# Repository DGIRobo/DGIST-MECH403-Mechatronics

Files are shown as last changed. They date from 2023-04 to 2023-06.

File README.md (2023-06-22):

# Pen Plotter for Blind People

**DGIST Undergradurate Student Jihwan Lee**

**DGIST Undergradurate Student Minhyeok Baek**

*Daegu Gyeongbuk Institute of Science and Technology (DGIST) Spring semester*

# **i**. Introduction

---

### 1. Project Topic:

시각장애인이 일반인들을 위해 제공되는 자료를 읽고 쓰게 할 수 있는 서비스를 제공하기 위한 음성기반 상호작용이 가능한 Pen Plotter의 개발.

### 2. Project Background:

지금까지 점자표지판, 점자 민원, 말하는 간행물 등 시각장애인을 위한 많은 서비스들이 만들어져 왔고, 이러한 서비스들은 실제로 공공기관에서 활용하고자 적극적으로 도입되어 왔습니다. 하지만, 이러한 대부분의 서비스는 사용자들을 배려하지 않아 완성도가 떨어지거나 공공기관에 도입한 이후에 제대로 서비스를 유지하고 관리하지 않아 사실상 활용도가 크게 떨어지는 문제점들을 가지고 있었습니다.

- 선행연구 1: 인쇄물음성변환출력코드(‘보이스아이’)
    
    말하는 공문서, 말하는 간행물과 같은 경우, 공공기관이 발행되는 간행물에 문서에 담긴 글과 미디어파일 등을 압축 저장한 일종의 바코드인 인쇄물음성변환출력코드(일명 ‘보이스아이’)를 첨부하여 제공하면, 시각장애인이 전용 스캐너를 사용해서 이 코드를 스캔해서 제공된 글이나 미디어를 볼 수 있게 해주는 서비스입니다. 이 서비스는 2009년 기준 대한민국 전자정부(G4C) 인터넷 민원서류 130여종과 보건복지부, 문화체육관광부 등 정부부처, 헌법재판소, 국가인권위원회, 서울시청, 서울 강남, 송파, 용산, 종로구청, 부산시청, 제주도청에서 도입되었고 전기요금고지서와 서울시수도요금고지서, 전국 지방세 고지서에서 사용되고 있다고 합니다. 하지만 이 서비스는 2009년 CBS 뉴스와 한국장애인문화협회 소리샵 센터가 공동 비교 분석한 결과 애당초 코드 자체가 읽히지 않거나 시각장애인들이 이해하기 어려울 정도로 잘못 편집된 경우가 많았다고 합니다. [1]
    
- 선행연구 2: 점자민원 서비스
    
    또한 점자 민원과 같은 경우, 공공기관이 발행되는 일반 간행물의 문서에 담긴 글과 미디어파일 등을 점자로 번역하여 시각장애인을 위한 간행물을 따로 제공하면, 시각장애인이 이 점자를 통해 제공된 글이나 미디어를 읽어볼 수 있게 해주는 서비스입니다. 이 서비스는 2016년 만들어진 점자법에 따라 현재 전국의 모든 공공기관이 도입하고 있습니다. [2]
    
    하지만 2020년에 진행된 대구대학교 한국특수교육문제연구소의 연구에 따르면 많은 시각장애인들은 이 서비스에 대해 잘 인지하고 있지 못하고 있고, 심지어 알고 공공기관에 요청함에도 불구하고 서비스를 받을 수 없었다고 합니다. [3][4]

때문에 이런 많은 서비스가 있음에도 불구하고 현재까지 시각장애인들은 보조인을 대동하여 민원 신청을 하거나 본인에게 필요한 정보를 찾아보는 것이 대한민국의 시각장애인의 현실입니다.

### 3. Problem Statement:

한 문장으로 정리하면, 공공기관에서 정보를 시각장애인이 인지할 수 있게 많은 서비스를 제공중임에도 시각장애인들은 공공기관의 홍보가 부족하여 이런 서비스들을 인지하지 못하고 있거나, 심지어는 공공기관에서 시각장애인들을 위한 서비스를 적절하게 제공하지 못하고 있는 문제로 인해 시각장애인들은 기본권인 “국민이 정부에 대한 일반적 정보공개를 구할 권리(청구권적 기본권)”과 “주민이 행정 기관에 원하는 바를 요구하는 일(민원)”을 보장받지 못하고 있습니다.

### 4. Approach:

따라서 우리는 공공기관에서 정보를 시각장애인이 인지할 수 있게 이런 많은 서비스를 제공중임에도 제대로 활용되고 있지 못하는 현 상황을 타개하고자. 시각장애인이 일반인들을 위해 제공되는 자료를 로봇을 통해 대리로 읽고 쓰게 할 수 있는 서비스를 만들고자 합니다.

- For Reading
    
    시각장애인이 일반인들을 위해 제공되는 자료를 로봇을 통해 대리로 읽고 쓰게 할 수 있는 서비스를 만들기 위해 우리는 우선 제공되는 자료를 카메라를 통해 보고 이것을 시각장애인이 받아들일 수 있는 감각을 통해 전달하는 기능이 필요하다는 것을 생각했습니다.
    
    일반적으로 시각장애인에게 정보를 전달할 수 있는 수단이라 하면, 대부분 점자와 음성을 떠올릴 것입니다. 하지만 한국의 점자 사용실태에 대해 추가로 조사한 결과, 한국시각장애교육&재활학회에서 발표된 조선대학교의 2015년 연구에서 표본 1000명 중 60%에 가까운 584명이 점자 사용을 하지 않고 있다는 것과, 이 중 100명은 음성지원 보조공학기기를 선호해서, 200명은 점자가 너무 어렵고 읽는 속도가 느려서 사용하지 않고 있다는 것을 확인하였습니다. 이 조사결과를 참고하여 시각장애인이 더 선호하는 음성서비스를 채택하기로 하였습니다. [5]
    
- For Writing
    
    시각장애인이 일반인들을 위해 제공되는 자료를 로봇을 통해 대리로 읽고 쓰게 할 수 있는 서비스를 만들기 위해 우리는 다음으로 시각장애인과 소통하여 시각장애인의 요구를 글로써 적을 수 있는 기능이 필요하다는 것을 생각했습니다. 일반적으로 시각장애인의 요구를 글로써 적을 수 있는 수단은 대부분 프린터를 떠올리겠으나 프린터는 단독적으로 사용될 수 없고 유지 보수에 있어서 많은 비용이 들기 때문에 부적합하다고 판단했습니다. 이 점으로 미루어볼 때, 유지 보수에 큰 비용이 들지 않는 저예산의 로봇팔을 채택하기로 하였습니다.

따라서 우리는 구체적으로 글자를 인식할 수 있는 카메라와 글자를 쓸 수 있는 펜 로봇을 조합하고, 음성기반 상호작용이 가능한 Pen Plotter라는 제품을 개발하는 접근법을 통해 이 문제를 해결하고자 했습니다.

# **ii**. Method

---

# 1. Hardware Design

Pen Plotter는 다음과 같이 설계되었습니다.

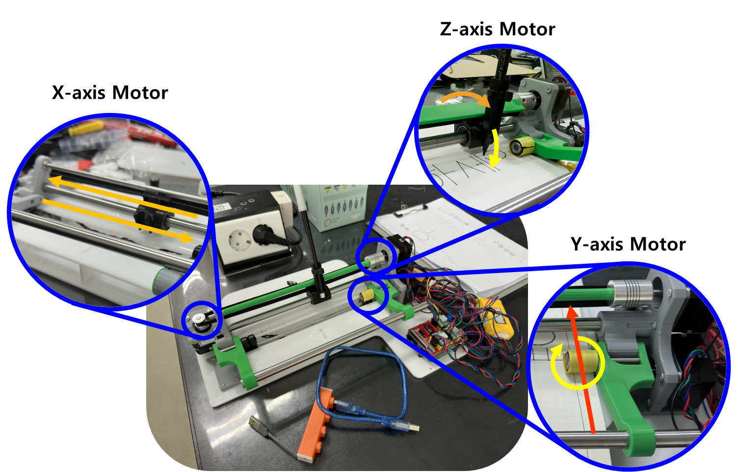
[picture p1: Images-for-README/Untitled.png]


기존의 x-y axis를 이동하는 Pen Plotter와는 다르게, y축 움직임을 롤러로 대체하여 공간의 컴팩트함을 강조하였습니다. 또한 모든 몸체와 하우징을 3D프린터와 레이저커터를 사용해 조립 가능한 형태로 제작함으로써, 교체 및 수리의 용이성과 제작의 간편함을 추구하였습니다. 바닥면의 경우 아크릴을 사용하여 바닥과의 마찰을 최소로 함과 동시에 평탄함을 잡았습니다. 각 구조에 대해 디테일하게 설명하도록 하겠습니다.

## 1-1) Base design

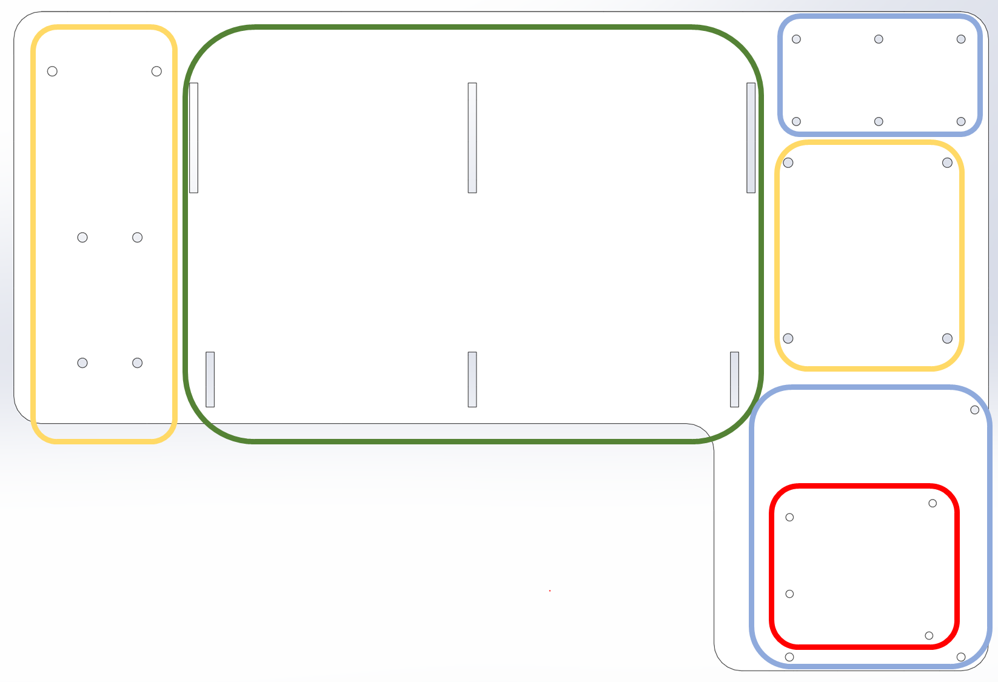
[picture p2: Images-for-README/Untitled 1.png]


 틀이 되는 베이스 부분입니다. 기본적으로 조립이 용이하도록 타공 형식으로 나사를 체결할 수 있도록 제작하였으며, 제일 basic한 M3 나사로 체결합니다. 실제 조립에는 진동이나 기타 이동으로 풀리지 않도록 spring washer를 사용해 진동 및 기타 disturbance에 영향을 받지 않도록 조립하였습니다.

각 타공된 구멍에 따른 역할은 다음과 같습니다.

> Yellow: Plotter base
Green: Paper base
Red: Circuit hole
Blue: Wire holder+Case
> 

3mm 아크릴로 제작하였으며, E5의 레이저커터를 사용해 제작했습니다.

## 1-2) X-axis side

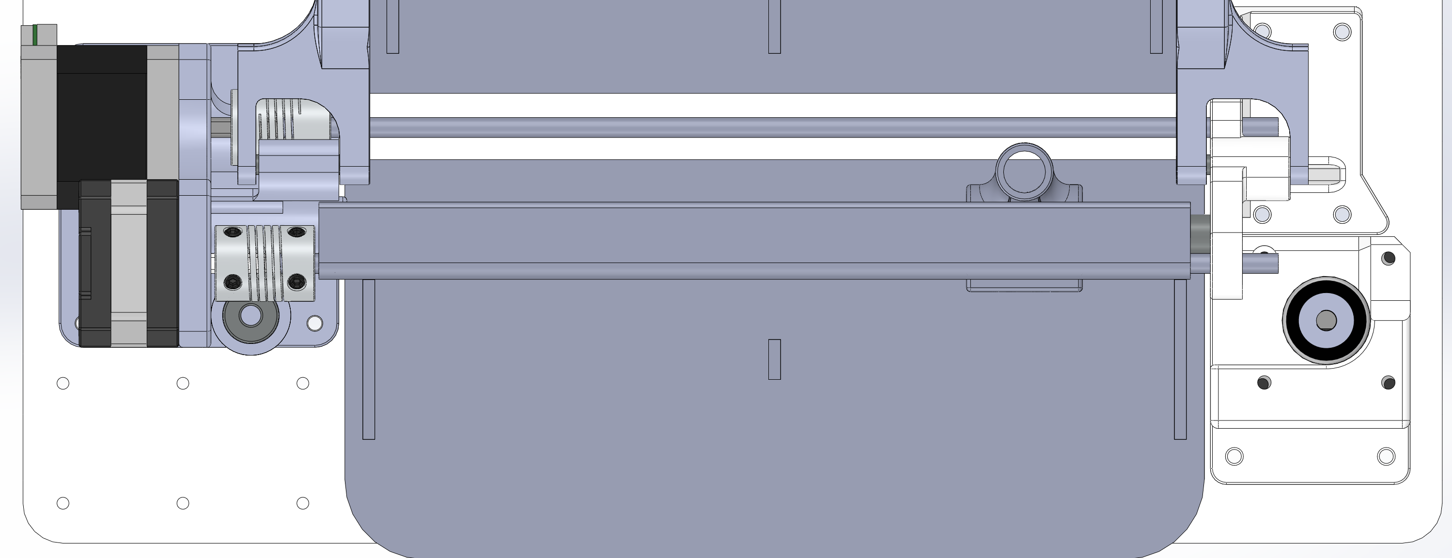
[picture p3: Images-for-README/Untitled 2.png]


X축의 경우, belt를 사용한 일반적인 plotter의 방식을 사용하였습니다. belt만 가지고는 고정력이 부족하기 때문에, 10mm 연마봉을 사용하여 pen을 지지하였습니다. 이 경우 연마봉과 pen 지지대 사이의 마찰력이 움직임에 영향을 줄 수 있기 때문에, ball bush를 사용하여 마찰력을 상쇄하였습니다.



Belt와 pen 지지대는 M3 나사로 체결하여 나사가 belt를 눌러주어 이동에 영향이 가지 않도록 디자인하였습니다.

X축의 최소 이동 거리의 경우, NEMA 17모터의 최소 step이 1.8도이고, 사용한 풀리의 잇수가 20입니다. 따라서 이를 계산하여 보면, 250step 기준으로 1.25바퀴를 회전하게 되고, 이는 25잇수만큼의 회전입니다. 부품의 각 이 간 거리가 2mm이므로, 250step : 50mm = 1step : xmm 를 계산하여 보면 1step = 0.2mm로 계산됩니다. 따라서 x resolution의 최소 단위는 0.2mm임을 알 수 있습니다.

## 1-3) Y-axis side

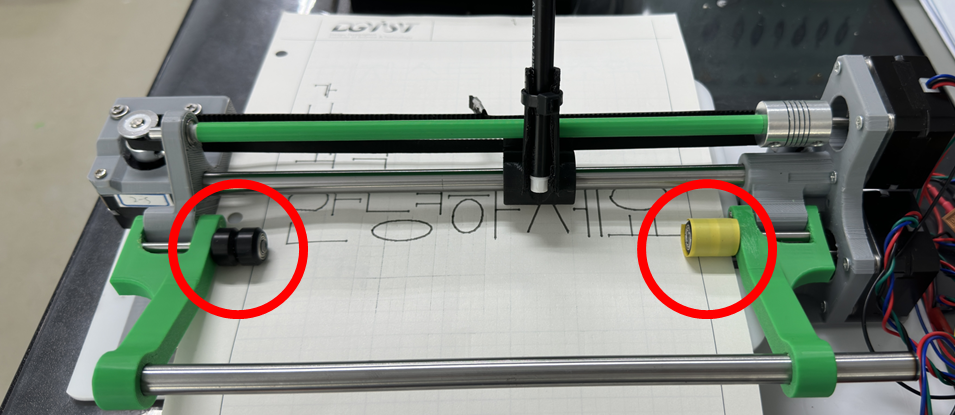
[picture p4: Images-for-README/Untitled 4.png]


Y축의 경우, roller를 사용하여 종이를 밀어주는 일반 잉크젯 프린터와 같은 방식을 차용하였습니다. roller는 저가 3D프린터에 주로 사용하는 roller bearing을 사용하였고, 단단한 고정 및 이동을 위해 양쪽에 2개씩, 위 아래로 한 쌍, 총 8개를 사용하여 종이를 단단하고 일정하게 밀어줄 수 있도록 하였습니다. 또한 손잡이를 10mm 연마봉으로 지지함으로써, 지레의 원리로 종이를 무겁게 눌러줌으로써 slip으로 인한 disturbance를 방지합니다.

그럼에도 실제 테스트 시에 종이가 slip하지 않을까 걱정되었지만, 사람이 잡고 있는 손이 끌려들어갈 만큼 slip은 충분하였습니다.

## 1-4) Z-axis side

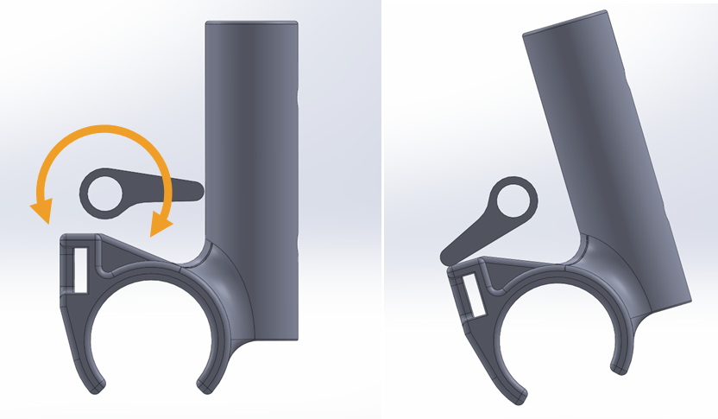
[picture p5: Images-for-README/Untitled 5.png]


기존의 돌기를 Z-axis의 lifter가 밀어 펜을 움직이는 방식과 달리, pen 자체를 밀어 움직이도록 하였습니다. 따라서 디자인의 컴팩트함을 더 올렸고, 단순히 belt의 tension으로 pen을 원위치 시키는 것이 아닌 두번째 사진처럼 종이에서 떨어질 때에는 반대방향으로 회전하여 pen을 고정시킴으로써 pen이 앞으로 쏠려 종이에 닿거나 진동으로 인해 종이에 닿는 상황을 막아줍니다. 이는 출력부의 회전을 고정시켜 출력시에 더 안정적으로 이동할 수 있게 해줍니다.

## 1-5) Other details

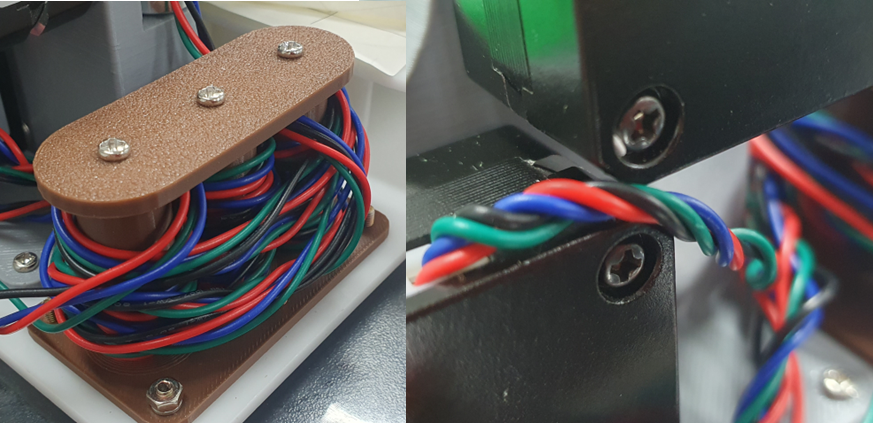
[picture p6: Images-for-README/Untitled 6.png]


뒷 부분에는 긴 wire들을 수용할 수 있도록 wire holder를 제작하였습니다. 세 축(X Y Z)의 전선들을 각각 수용할 수 있어 추후 점검이나 부품 교체에 용이하도록 설계하였습니다. 이 역시 spring washer로 조립되어 안정성을 높였습니다. 각 wire들은 unshielded twisted pair로 꼬아 놓음으로써 발생할 수 있는 noise나 간섭에 대해서도 보강하였습니다.

또한 본 시스템의 경우 CNC나 여타 pen plotter에 사용되는 endstop switch가 존재하지 않습니다. 이는 의도한 것으로, endstop 스위치가 가지는 불편한 점을 개선하기 위해 일부러 넣지 않았습니다. 이에 대한 이유는 Software design의 Gcode 부분에서 서술하겠습니다.

# 2. Software Design

다음으로 위와 같은 Hardware를 구동하는 Software는 아래 그림과 같이 설계되었습니다. 

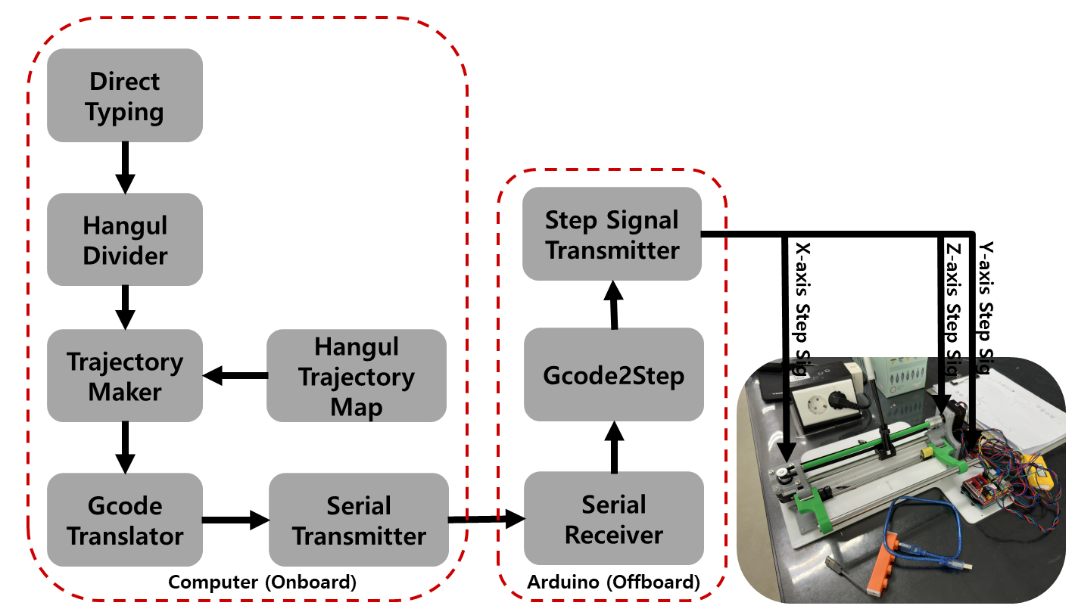
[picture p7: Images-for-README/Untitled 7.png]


전체적인 Algorithm을 요약해서 설명하자면 다음과 같습니다. 사용자가 컴퓨터에 키보드를 이용해서 한글 문장을 입력하면 Computer는 그 한글 문장을 자모 단위까지 분리하고 자모 Trajectory를 참조해서 글자 하나부터 문장까지 정규화된 계산 방식을 사용해서 차근차근 결합시켜서 하나의 Trajectory를 만들어냅니다. 그리고 Computer는 이 Trajectory를 Gcode 양식으로 변환해서 Serial 통신을 통해 Arduino에 송신합니다. 그러면 이제 Arduino는 Computer로부터 Serial 통신을 통해 들어온 Gcode 양식의 Trajectory를  Step 단위로 바꿔서 각 X축, Y축, Z축 Step 모터를 해당 Step 만큼 움직이는 것을 제어하는 것으로 사용자가 입력한 문장을 A4 종이에 대필하는 것을 수행할 수 있게 됩니다.

이때 설명한 Computer가 수행하는 구체적인 연산은 모두 객체화되어 있습니다. 첫번째로 사용자가 입력한 한글 문장을 한글의 자모 단위까지 분리하고 한 글자 마다 Type을 부여하는 Algorithm은 Hangul Divider라는 이름으로 객체화되어 있습니다. 두번째로 자모 데이터를 참조해서 자모 Trajectory를 추출하는 Algorithm은 Hangul Trajectory Map이라는 이름으로 객체화되어 있습니다. 세번째로 자모 Trajectory를 조합해서 한 문자, 한 단어, 문장까지 이어서 조합하는 Algorithm은 Trajectory Maker라는 이름으로 객체화되어 있습니다.

## 2-1) Hangul Divider Algorithm

앞서 소개했듯 사용자가 입력한 한글 문장을 한글의 자모 단위까지 분리하고 한 글자 마다 Type을 부여하는 Algorithm은 Hangul Divider라는 이름으로 객체화되어 있습니다. 이 Hangul Divider는 [6]에서 소개하는 Algorithm을 펜 플로터 Trajectory 생성을 위해 Concept만 반영하고 다르게 구현된 방식입니다. [6]의 설명에 따르면 한글 unicode에는 아래 사진과 같은 규칙이 있습니다.

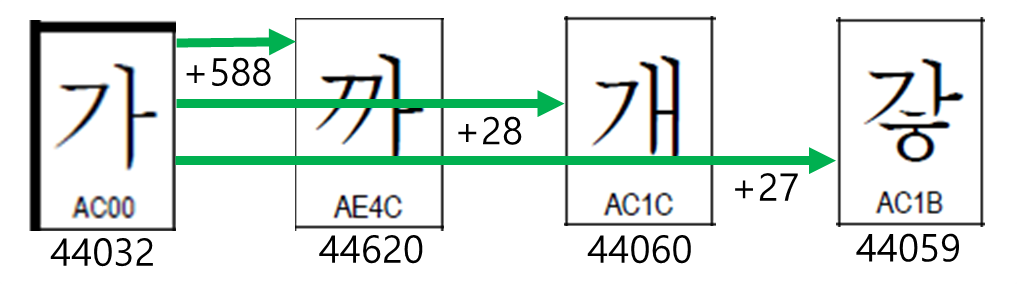
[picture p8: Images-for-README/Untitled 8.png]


우선 한글 unicode는 초성이 588 문자마다 바뀝니다. 이는 즉 한글 unicode를 588로 나누면 그 한글의 초성을 추출할 수 있다는 것을 의미합니다. 또한 한글 unicode는 중성이 같은 초성일 때 28 문자마다 바뀝니다. 이는 즉 한글 unicode에서 초성을 추출한 후 unicode에서 초성값에 588을 곱한 값을 빼주고 28로 나누면 그 한글의 중성을 추출할 수 있다는 것을 의미합니다. 종성도 마찬가지로 초성과 중성이 같을 때 28개가 존재합니다. 따라서 한글 unicode에서 초성을 추출한 후 unicode에서 초성값에 588을 곱한 값을 빼주고 중성값에 28을 곱한 값을 빼주고 28로 나누면 종성을 추출할 수 있습니다. 따라서 Hangul Divider Algorithm은 이를 반영하여 입력된 문장을 글자 하나 하나로 나누고 글자 하나 하나를 초성 중성 종성으로 또 한번 나눕니다.

거기에 Hangul Divider Algorithm은 Trajectory 형성을 위해 한글의 형태에 대한 정보를 분리한 초성 중성 종성 정보에 추가하여 리턴합니다. 한글은 중성이 세로형인지 가로형인지 이중모음인지에 따라 3가지 Type으로 구분되고 각각의 Type은 종성이 있는가에 따라 다시 2가지 Type으로 구분되기 때문에 Hangul Divider Algorithm은 한글의 모양을 다음의 6가지로 정형화 합니다.

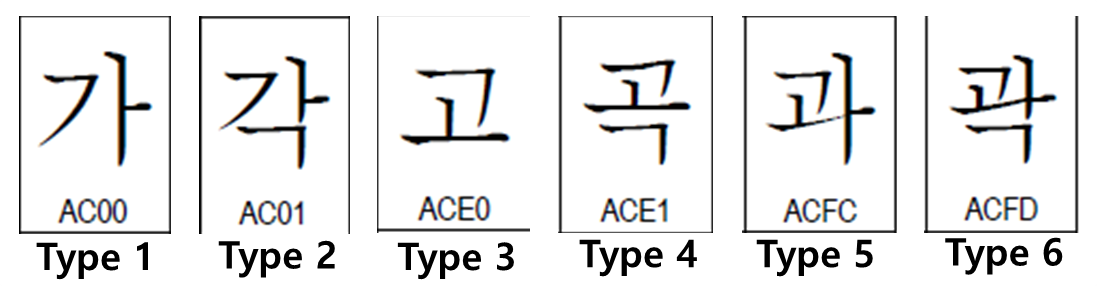
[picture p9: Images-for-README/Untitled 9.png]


이러한 Hangul Divider Algorithm의 Pseudocode는 다음과 같이 정리됩니다.

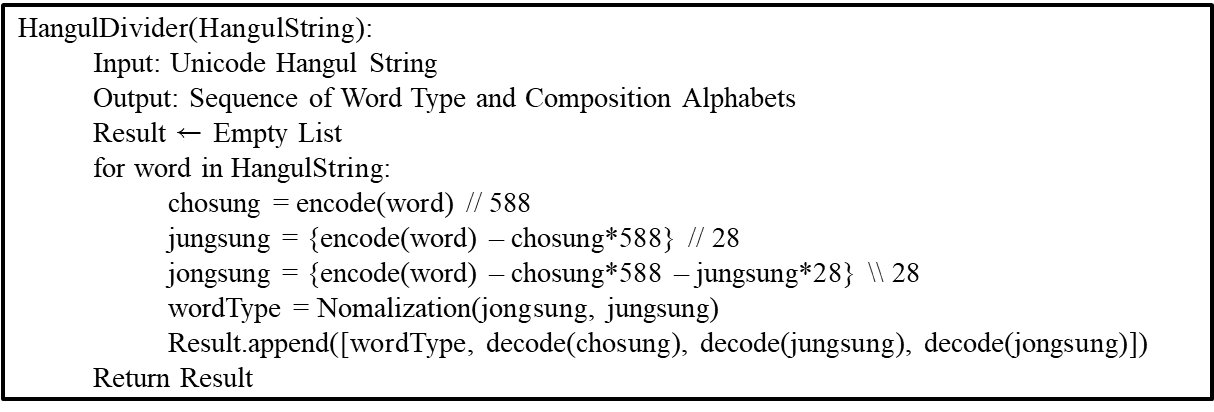
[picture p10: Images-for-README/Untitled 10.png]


따라서 이러한 Hangul Divider Algorithm을 실행하면 다음과 같이 문장을 글자 단위로 한번, 초성 중성 종성 단위로 한번 더 분리해주는 기능을 수행해준다는 것을 확인할 수 있습니다.



## 2-2) One Word Making Algorithm

앞서 소개했듯 자모 데이터를 참조해서 자모 Trajectory를 추출하는 Algorithm은 Hangul Trajectory Map이라는 이름으로 객체화되어 있고, 자모 Trajectory를 조합해서 한 문자, 한 단어, 문장까지 이어서 조합하는 Algorithm은 Trajectory Maker라는 이름으로 객체화되어 있습니다. 이 두 Algorithm이 이어져서 한글 한 글자 Trajectory를 만드는 과정은 다음과 같습니다.

우선 Hangul Trajectory Map Algorithm은 Hangul Divider Algorithm에서 분리된 초성 중성 종성을 참조하여 각 문자를 Trajectory로 치환해줍니다. 이때 Hangul Trajectory Map Algorithm은 아래 그림과 같은 초성 Map, 중성 Map, 종성 Map을 보조 자료구조로서 가지고 있기 때문에 이 Map들을 이용해서 초성 중성 종성을 참조하여 각 문자를 Trajectory로 치환하게 됩니다.

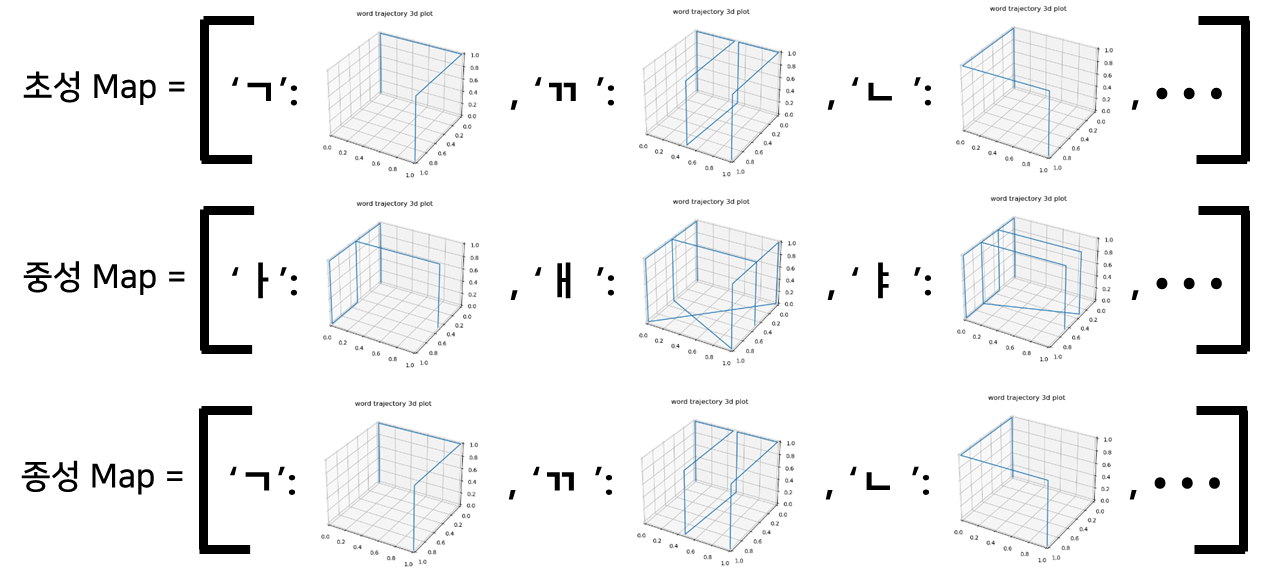
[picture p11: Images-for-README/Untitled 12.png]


Hangul Trajectory Map Algorithm이 각 문자를 Trajectory로 치환하면 다음으로 Trajectory Maker Algorithm은 Hangul Divider Algorithm의 결과값 중에서 해당 글자의 Type을 조회합니다. Trajectory Maker Algorithm은 이 Type에 따라서 아래 사진과 같이 자모 Trajectory를 resize하고 offset을 설정하고 합쳐줌으로써 하나의 글자 Trajectory를 만들어냅니다.

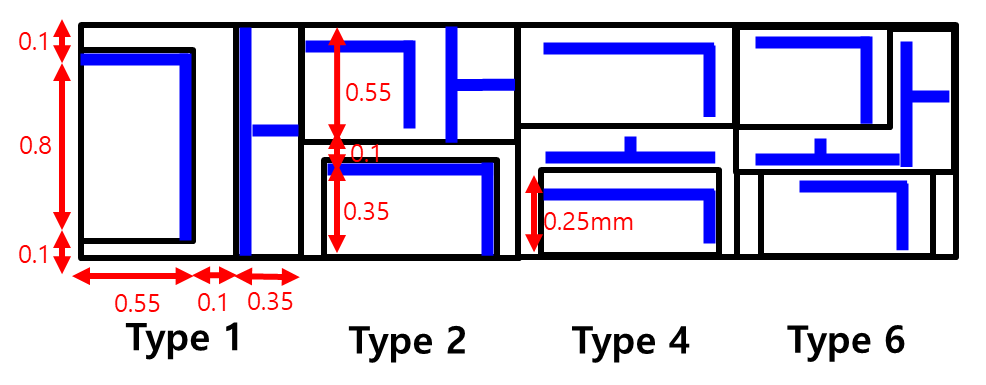
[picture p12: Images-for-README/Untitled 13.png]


이러한 Trajectory Maker Algorithm에서 Type 1 글자의 Trajectory를 생성하는 function의 Pseudocode는 다음과 같이 정리됩니다.

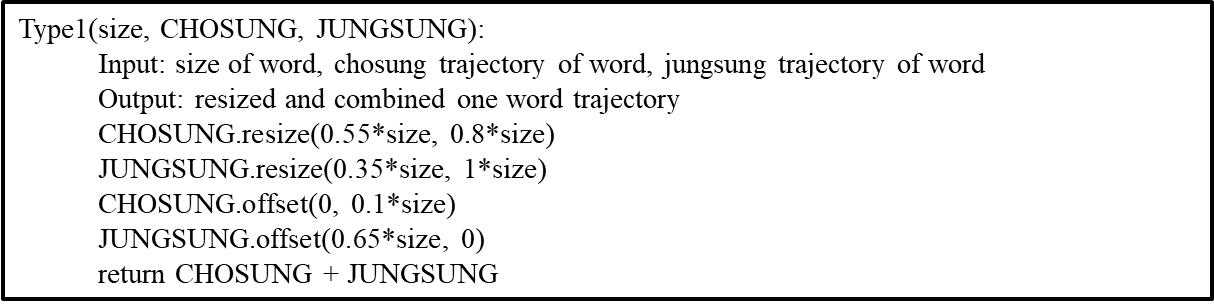
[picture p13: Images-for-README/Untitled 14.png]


## 2-3) String Making Algorithm

그러면 이제 Hangul Trajectory Map Algorithm과 Trajectory Maker Algorithm이 한글 한 글자 Trajectory를 만드는 과정을 알아보았으므로, Trajectory Maker Algorithm이 이러한 한 글자 한 글자들이 이어진 단어 및 문장 Trajectory를 어떻게 만들어내는지 알아보도록 합니다. Trajectory Maker Algorithm에서 이러한 한 글자 한 글자들이 이어진 단어 및 문장 Trajectory를 만드는 StringTrajectoryMaking function의 Pseudocode는 다음과 같습니다.

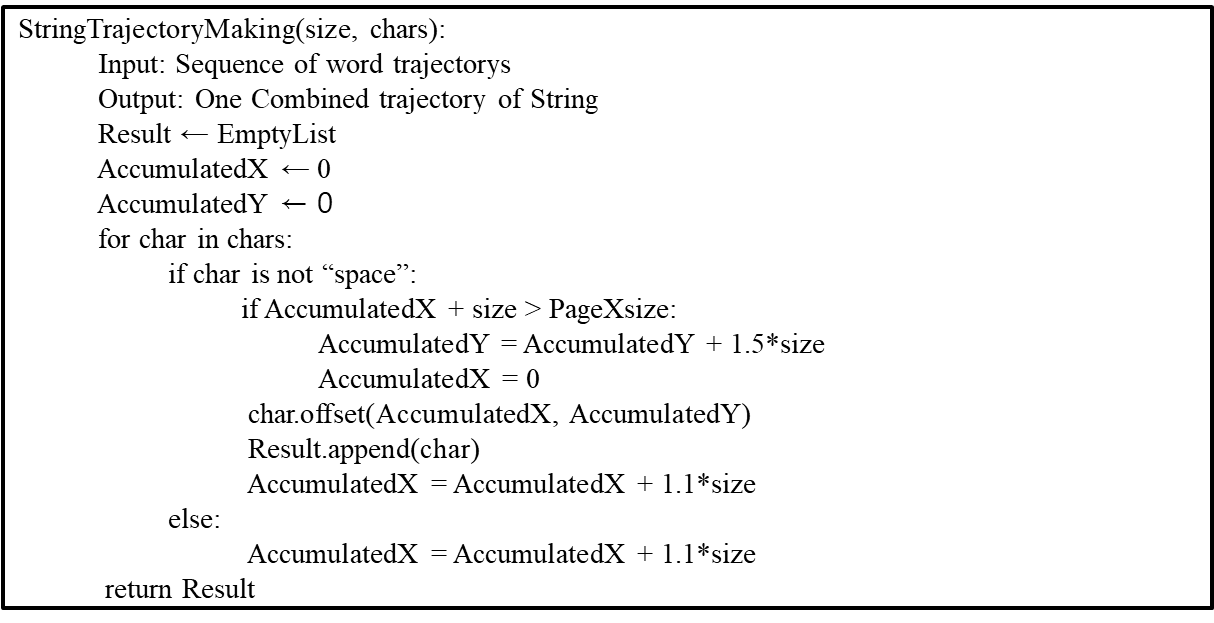
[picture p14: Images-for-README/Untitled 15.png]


Pseudocode를 보면 확인할 수 있듯 Trajectory Maker Algorithm은 사람이 글씨를 쓰는 것과 상당히 비슷한 방식으로 글씨 Trajectory를 생성합니다. 구체적으로 말하자면 한 글자를 쓰면 그 글자의 가로 크기 만큼 X축으로 이동하여 새 한 글자를 작성하도록 Pseudocode가 만들어져 있습니다. 이때 글자를 X축으로 어느 정도나 이동시켜서 작성할지에 관한 정보는 AccumulatedX라는 변수가 담당하여 계산합니다. 그런데 이 AccumulatedX가 Page의 최대 X길이를 넘어가면 사람이 글을 쓸 때 가로줄을 한줄 다쓰면 줄바꿈을 해서 새 줄을 쓰듯 AccumulatedY가 한 글자 크기만큼 누적되고 accumulatedX가 0부터 다시 출발하도록 되어 있습니다. 이에 따라 단순한 한 글자이던 한 단어이든 한 문장이던 여러 문장이던 상관없이 작성 문서 규격을 고려한 Trajectory를 생성할 수 있다는 것을 알 수 있습니다.

따라서 이러한 String Making Algorithm을 실행하면 다음과 같이 문장에 대응하는 Trajectory를 작성 문서 규격을 고려해서 생성해준다는 것을 확인할 수 있습니다.

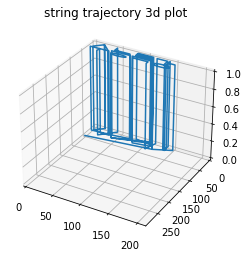
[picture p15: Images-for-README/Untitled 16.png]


## 2-4) Auto Word-Wrap

그런데 지금까지의 Algorithm은 한번 입력받으면 그 한번 입력받은 문장에 대해서만 작성을 완료하면 모든 작업이 완료되도록 만들어져 있습니다. 우리가 최종적으로 만들고자 하는 펜 플로터가 지속적으로 사용자와 상호작용하면서 사용자가 쓰고 싶은 단어를 계속 써주는 것임을 생각해보면 한번 입력받은 문장에 대해서 작성을 완료하면 다음 입력받을 문장을 이어서 작성할 수 있는 추가적인 Algorithm이 필요합니다. 따라서 만들어진 것이 다음그림과 같은 Tree Diagram에 따라 작동하는 Auto Word-Wrap Algorithm입니다.

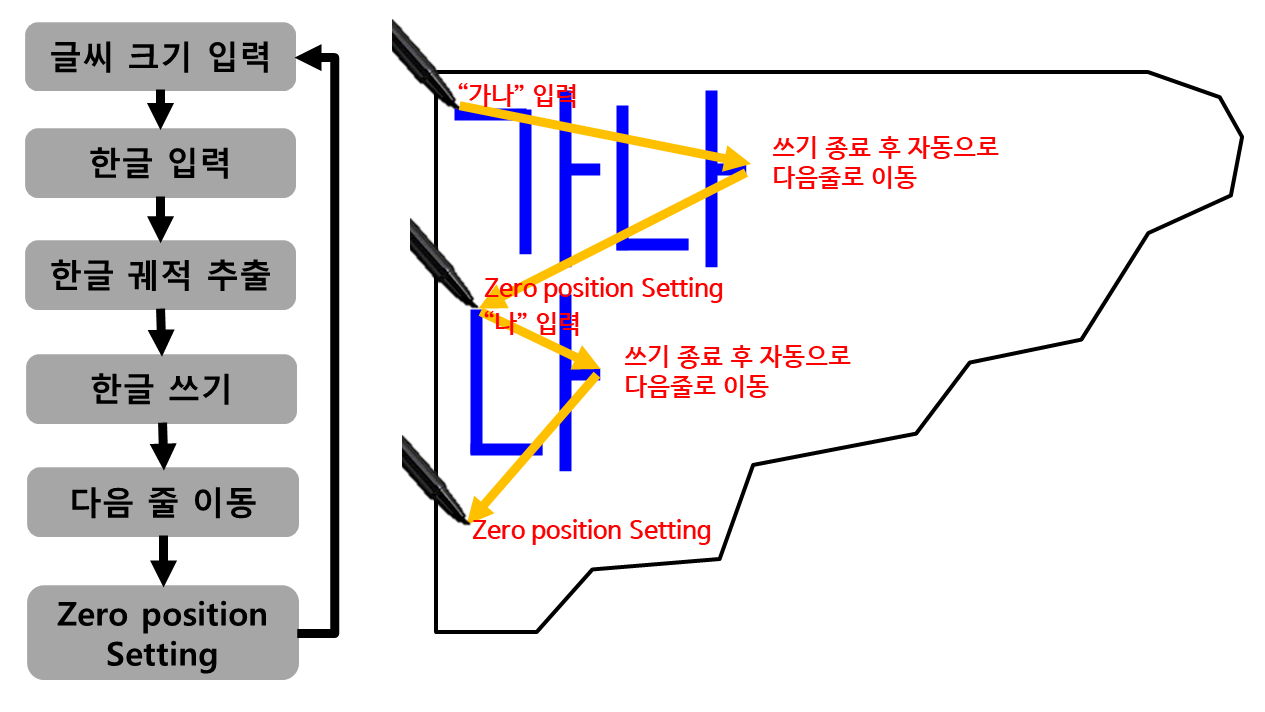
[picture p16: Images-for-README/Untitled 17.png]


이 Auto Word-Wrap Algorithm은 한번 입력 받은 문장에 대해 작성을 완료하면 자동으로 줄바꿈을 해서 다음 입력받을 문장을 쓸 준비를 하도록 하는 Algorithm입니다. 이 Algorithm은 Trajectory 형성 단계에서 Trajectory의 마지막 점을 (0, AccumulatedY+1.5*size)로 하여 줄바꿈을 구현하고 이동을 완료했을 때, Zero position setting을 의미하는 Gcode를 Arduino에 전송하는 것으로 시작점을 (0,0)으로 하는 다음 입력받을 문장을 이어서 작성할 수 있도록 구현되었습니다. 그 결과 한번 입력 받은 문장의 작성을 완료하면 다음 줄로 넘어가서 새로 작성할 문장을 입력받고 새로 작성할 문장을 작성한 이후에도 지속적으로 사용자의 문장을 받아 대필하는 작업을 수행할 수 있게 되었습니다.

## 2-5) Gcode

이러한 작업들을 수행하기 위해, Gcode를 새롭게 재설정하였습니다.

기존 pen plotter들의 경우 endstop switch를 사용하여 현재 절대 좌표를 지정한 후 그 이후 움직이는 장점을 가집니다. 이는 원하는 위치에서 출력할 때는 큰 문제가 되지 않지만, 간단히 문서에 작성하는 pen plotter를 지향하는 본 프로젝트에 적합하지 않다 판단하였습니다. 사용자가 원하는 위치에 바로 pen을 가져가 그 위치에서 바로 출력할 수 있는 것이 더 적합하여, 본 프로젝트에서는 현재 위치를 (0,0) 으로 가지는 Gcode protocol을 설정하였습니다.

```python
if Event == 0:
        s.write(('F500' + '\n').encode())
        s.write(('G21' + '\n').encode())
        s.write(('$100 = 5' + '\n').encode()) # x offset 5step = 1mm for y-axis
        s.write(('$101 = 5' + '\n').encode()) # y offset 5step = 1mm for y-axis
        s.write(('$102 = 10' + '\n').encode()) # z offset 5step = 1mm for y-axis
        s.write(('G92 X0 Y0' + '\n').encode())
        s.write(('G04 p0.5\n').encode())
    Event = Event + 1
    
    for dotIndex in range(len(Gcode)):
        s.write((Gcode[dotIndex] + '\n').encode())
        print('Sending: ' + Gcode[dotIndex])
        grbl_out = s.readline() # Wait for grbl response with carriage return
        print(' : ' + grbl_out.strip().decode())
        print('Sending: G04 p0.5\n')
        s.write(('G04 p0.5\n').encode())
        grbl_out = s.readline() # Wait for grbl response with carriage return
        print(' : ' + grbl_out.strip().decode())
    s.write(('G92 X0 Y0' + '\n').encode())
```

G92 항을 추가하여 현재 위치를 (0,0)으로 재설정하며, 출력이 끝난 이후에도 이를 한번 더 반복해 이후 출력에도 똑같이 대응할 수 있게 하였습니다.

```python
def Trajectory2Gcode(trajectory):
    for dotIndex in range(len(trajectory)):
        trajectory[dotIndex] = f"G90 X{round(trajectory[dotIndex][0], 4)} Y{round(5/6*trajectory[dotIndex][1], 4)} Z{1-z_offset*float(trajectory[dotIndex][2])}"
    return trajectory
```

또한 글씨 출력 시 절대좌표로 이동하는 G01을 사용하지 않고 현재 상태에서 이동하는 G92를 사용하였습니다. 따라서 본 작업을 통해 endstop swtich 없이도 더욱 직관적으로 Pen Plotter를 작동시킬 수 있었습니다.

# **iii**. Results

---

위와 같은 Concept를 통해 개발된 펜 플로터를 사용해 다음과 같은 총 4가지 Test를 계획, 진행하였습니다.

### 1. One Word Writing Test

첫번째로 진행한 Test는 원하는 글씨의 크기와 한글 한 글자를 입력했을 때, 펜 플로터가 그 글씨를 정확하게 쓸 수 있는지에 대해 검증하는 실험이었습니다. 이 실험에서는 글자 크기를 10mm로 하고 ‘가’를 입력하였습니다. 그 결과는 아래 사진과 같이 나왔습니다. 이를 통해 본 프로젝트에서 만든 펜 플로터가 입력된 궤적을 큰 오차없이 정확하게 그려내는 것이 가능하다는 것을 검증할 수 있었습니다.

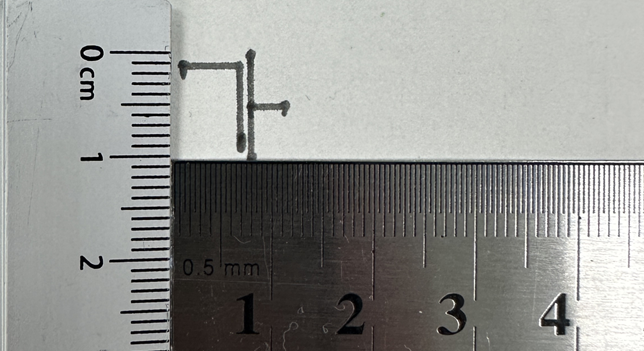
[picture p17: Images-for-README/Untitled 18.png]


### 2. Multi Word Writing Test

두번째로 진행한 Test는 원하는 글씨의 크기와 한글 한 단어를 입력했을 때, 펜 플로터가 그 단어를 정확하게 쓸 수 있는지에 대해 검증하는 실험이었습니다. 이 실험에서는 글자 크기를 20mm로 하고 ‘과곽’을 입력하였습니다. 그 결과는 아래 사진과 같이 나왔습니다. 이를 통해 본 프로젝트에서 만든 펜 플로터는 한글 두 글자 이상의 단어도 큰 Compuation 문제 없이 처리할 수 있고 입력받은 글자 크기를 반영해서 자유롭게 출력이 가능하다는 것을 검증할 수 있었습니다.

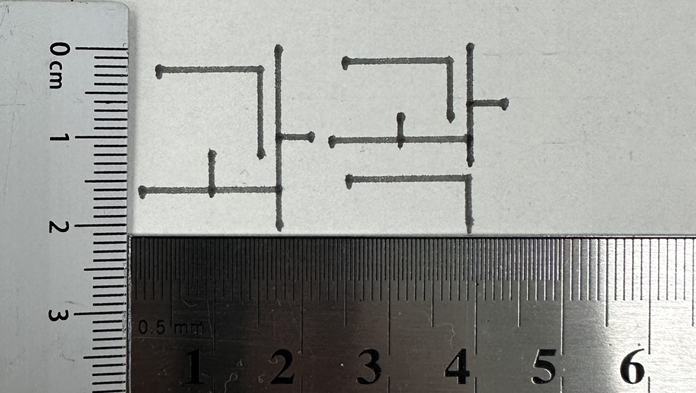
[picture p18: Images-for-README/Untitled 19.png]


### 3. Word Spacing, Wrap Test

세번째로 진행한 Test는 원하는 글씨의 크기와 한글 한 문장을 입력했을 때, 펜 플로터가 그 문장을 띄어쓰기를 구분하고 자동으로 줄바꿈을 진행하며 정확하게 써내려갈 수 있는지에 대해 검증하는 실험이었습니다. 이 실험에서는 글자 크기를 20mm로 하고 ‘디지스트 기초학부’를 입력하였습니다. 그 결과는 아래 사진과 같이 나왔습니다. 아래 사진을 보면 ‘트’와 ‘기’ 사이에 한 글자 만큼의 space를 정상적으로 반영해서 글자를 작성한 것을 확인할 수 있고 ‘부’가 글자를 작성할 수 있는 범위인 160mm를 넘어가자 그 다음 줄로 자동으로 줄바꿈을 해서 글자를 이어서 작성한 것을 확인할 수 있습니다. 이를 통해 본 프로젝트에서 만든 펜 플로터는 문장 단위도 큰 Compuation 문제 없이 처리할 수 있고 문장이 한 줄 이상을 써야하게 되는 경우에도 자동으로 줄바꿈을 해서 무리없이 모든 문장을 출력할 수 있다는 것을 검증할 수 있었습니다.

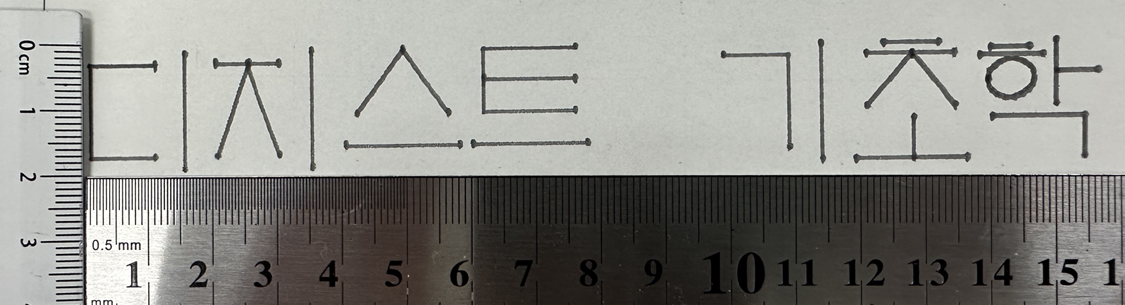
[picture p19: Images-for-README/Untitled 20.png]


### 4. Accuracy Test

네번째로 진행한 Test는 같은 위치에서 같은 한글 한 글자를 반복해서 작성할 때 어느 정도로 오차가 누적되어 글씨가 밀리게 될 것인지를 확인하기 위한 실험이었습니다. 이 실험의 결과는 아래와 같이 나왔습니다. 좌측의 사진은 1cm ‘가’를 입력받았을 때 그 글자를 한번만 작성한 결과이고 우측의 사진은 1cm ‘가’를 입력받았을 때 같은 자리에서 3번 그 글자를 작성한 결과입니다. 육안으로 봐도 확실하게 알 수 있듯 정확하게 전혀 오차 없이 같은 자리에서 글자를 작성했다는 것을 확인할 수 있습니다. 이 결과로 미루어 볼 때, 본 프로젝트에서 롤러를 사용한 펜 플로터도 충분히 입력한 궤적을 정확하게 그려낼 수 있다는 것을 알 수 있습니다. 이는 기존의 다른 펜 플로터들이 종이에 글씨를 정확히 작성하기 위해 종이를 고정하고 펜 플로터를 종이 전체 위를 움직이면서 작성하는 대신 공간 효율성을 포기한 것을 본 프로젝트에서 만든 롤러를 사용한 펜 플로터로 개선할 수 있다는 것을 보여줍니다.

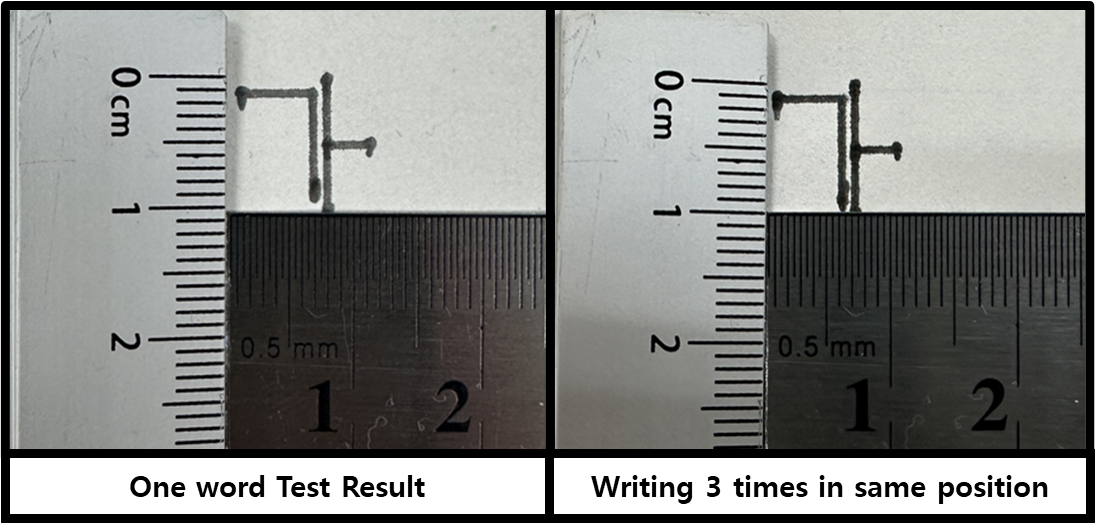
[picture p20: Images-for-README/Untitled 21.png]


# **iv**. Conclusion

---

### 1. Suggestion point of this project

이 프로젝트가 이루어낸 성과를 정리하자면 다음과 같습니다. 첫번째로 A4 용지 정도의 공간이 확보되어야 사용가능한 기존 펜 플로터와는 다르게 X축, Y축, Z축 모터와 축 부품을 최대한 근접하게 붙여서 설계하여 보다 협소한 공간에서도 작동할 수 있게 만들었습니다. 이는 본 프로젝트에서 제안하는 시각장애인이 관공서에서 공문서를 읽거나 공문서를 작성하는 것을 넘어 일상생활에서 시각장애인이 휴대하면서 문서작성이 필요한 경우에 항상 사용이 가능한 펜 플로터를 만들 수 있다는 가능성을 보여줍니다. 두번째로 영어나 숫자를 쓰는 것에 국한된 기존 펜 플로터들과는 다르게 본 프로젝트에서는 직접 개발한 한글 궤적을 만드는 라이브러리를 통해 펜 플로터가 한글 문장을 작성합니다. 이때 한글 궤적 라이브러리는 Encapsulation이 잘 되어 있고, 궤적을 Gcode값으로 리턴하기 때문에 본 프로젝트에서 만든 펜 플로터에 제한되지 않고 다른 펜 플로터들에도 적용하여 사용할 수 있다는 장점을 가지고 있습니다. 마지막으로 본 프로젝트에서 만든 펜 플로터는 사용자와 실시간 상호작용을 통해 글을 작성하고자 하는 목적에 따라 인터랙티브 입력창 기능과 글씨를 쓰는 펜의 위치를 사용자가 동적으로 변경할 수 있는 기능을 추가 및 구현하였습니다. 이는 인쇄를 시킨 다음에는 상호작용이 불가능한 잉크젯 프린터나 기존의 펜 플로터들과 명확히 구별되는 차이점입니다.

### 2. Points to Improve

하지만 이 프로젝트에서 만들어진 펜 플로터가 모든 면에서 장점을 가진 것은 아닙니다. 현재 본 프로젝트에서 개발한 펜 플로터는 높이가 15mm인 글자 7개를 쓰는데 15분이 걸릴정도로 쓰기 속도가 상당히 느립니다. 이는 개발 과정에서 글씨를 정확하게 쓰는데 집중하여 mm당 Step 수만 고려한 결과에 따라 발생한 문제로 추가로 Gcode를 수정하면 해결될 것으로 보입니다. 다만 속도를 빠르게 함에 따라 진동이 발생할 수 있기 때문에 차후 속도를 빠르게 함에 따라 발생하는 진동을 측정하고 이를 최소화하는 전략을 고안해야 할 것으로 보입니다. 또한 앞에서 이 펜 플로터는 쓰기 시작점을 수동으로 수정할 수 있다는 장점이 있다고 설명하였지만 쓰기 시작점을 수동으로 설정하면 자동 줄 바꿈 기능이 작동하지 않기 때문에 긴 텍스트를 입력하면 펜 플로터가 Task Space 외곽에 부딫혀 고장을 일으킬 가능성이 있습니다. 따라서 이를 해결하기 위해 추가로 End Stop 스위치나 Encoder를 부착하여 펜의 위치가 Task Space 상에서 어디에 위치하고 있는지 피드백해주는 것이 필요할 것으로 보입니다. 마지막으로 본 프로젝트는 터미널에 키보드로 입력한 한글 문장을 대필해주는 펜 플로터의 개발에 성공하였으나 본래 최종 목적은 음성으로 말한 한글 문장을 대필해주는 펜 플로터의 개발이었습니다. 이는 시각 장애인을 위한 시스템을 개발한다는 관점에서 가장 중요했던 기능이었습니다. 따라서 향후 추가될 예정에 있습니다.

# **v**. References

---

- [1].
    
    ['말하는 공문서' 오류 투성이...시각장애인 배려 시늉만](https://www.nocutnews.co.kr/news/4149138)
    
- [2].
    
    [시각장애인도 경찰서에서 쉽게 민원 신청한다](https://www.seoul.co.kr/news/newsView.php?id=20210906500051)
    
- [3].
    
    [시각장애인, 경찰에 ‘점자 통지’ 요청했지만…못 받은 이유는?](https://news.kbs.co.kr/news/view.do?ncd=5496433)
    
- [4]
    
    [시각장애인의 민원 정보 이용 실태와 요구 조사](https://www.kci.go.kr/kciportal/ci/sereArticleSearch/ciSereArtiView.kci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)
    
- [5]
    
    [시각장애인의 점자에 관한 인식과 점자 사용 실태](https://www.kci.go.kr/kciportal/ci/sereArticleSearch/ciSereArtiView.kci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)
    
- [6]
    
    [https://github.com/bluedisk/hangul-toolkit](https://github.com/bluedisk/hangul-toolkit)

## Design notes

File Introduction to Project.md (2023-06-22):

# Pen Plotter for Blind People

**DGIST Undergradurate Student Jihwan Lee**

**DGIST Undergradurate Student Minhyeok Baek**

***MECH404 final report***

*Daegu Gyeongbuk Institute of Science and Technology (DGIST) Spring semester*

# **i**. Introduction

---

### 1. Project Topic:

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

### 2. Project Background:

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

### 3. Problem Statement:

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

### 4. Approach:

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

# **ii**. Method

---

# 1. Hardware Design

Pen Plotter는 다음과 같이 설계되었습니다.



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

## 1-1) Base design



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

각 타공된 구멍에 따른 역할은 다음과 같습니다.

> Yellow: Plotter base
Green: Paper base
Red: Circuit hole
Blue: Wire holder+Case
> 

3mm 아크릴로 제작하였으며, E5의 레이저커터를 사용해 제작했습니다.

## 1-2) X-axis side



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



Belt와 pen 지지대는 M3 나사로 체결하여 나사가 belt를 눌러주어 이동에 영향이 가지 않도록 디자인하였습니다.

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

## 1-3) Y-axis side



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

그럼에도 실제 테스트 시에 종이가 slip하지 않을까 걱정되었지만, 사람이 잡고 있는 손이 끌려들어갈 만큼 slip은 충분하였습니다.

## 1-4) Z-axis side



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

## 1-5) Other details



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

# 2. Software Design

다음으로 위와 같은 Hardware를 구동하는 Software는 아래 그림과 같이 설계되었습니다. 



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

## 2-1) Hangul Divider Algorithm

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



이러한 Hangul Divider Algorithm의 Pseudocode는 다음과 같이 정리됩니다.



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



## 2-2) One Word Making Algorithm

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



이러한 Trajectory Maker Algorithm에서 Type 1 글자의 Trajectory를 생성하는 function의 Pseudocode는 다음과 같이 정리됩니다.



## 2-3) String Making Algorithm

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



## 2-4) Auto Word-Wrap

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

## 2-5) Gcode

이러한 작업들을 수행하기 위해, Gcode를 새롭게 재설정하였습니다.

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

```python
if Event == 0:
        s.write(('F500' + '\n').encode())
        s.write(('G21' + '\n').encode())
        s.write(('$100 = 5' + '\n').encode()) # x offset 5step = 1mm for y-axis
        s.write(('$101 = 5' + '\n').encode()) # y offset 5step = 1mm for y-axis
        s.write(('$102 = 10' + '\n').encode()) # z offset 5step = 1mm for y-axis
        s.write(('G92 X0 Y0' + '\n').encode())
        s.write(('G04 p0.5\n').encode())
    Event = Event + 1
    
    for dotIndex in range(len(Gcode)):
        s.write((Gcode[dotIndex] + '\n').encode())
        print('Sending: ' + Gcode[dotIndex])
        grbl_out = s.readline() # Wait for grbl response with carriage return
        print(' : ' + grbl_out.strip().decode())
        print('Sending: G04 p0.5\n')
        s.write(('G04 p0.5\n').encode())
        grbl_out = s.readline() # Wait for grbl response with carriage return
        print(' : ' + grbl_out.strip().decode())
    s.write(('G92 X0 Y0' + '\n').encode())
```

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

```python
def Trajectory2Gcode(trajectory):
    for dotIndex in range(len(trajectory)):
        trajectory[dotIndex] = f"G90 X{round(trajectory[dotIndex][0], 4)} Y{round(5/6*trajectory[dotIndex][1], 4)} Z{1-z_offset*float(trajectory[dotIndex][2])}"
    return trajectory
```

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

# **iii**. Results

---

위와 같은 Concept를 통해 개발된 펜 플로터를 사용해 다음과 같은 총 4가지 Test를 계획, 진행하였습니다.

### 1. One Word Writing Test

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



### 2. Multi Word Writing Test

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



### 3. Word Spacing, Wrap Test

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



### 4. Accuracy Test

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



# **iv**. Conclusion

---

### 1. Suggestion point of this project

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

### 2. Points to Improve

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

# **v**. References

---

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

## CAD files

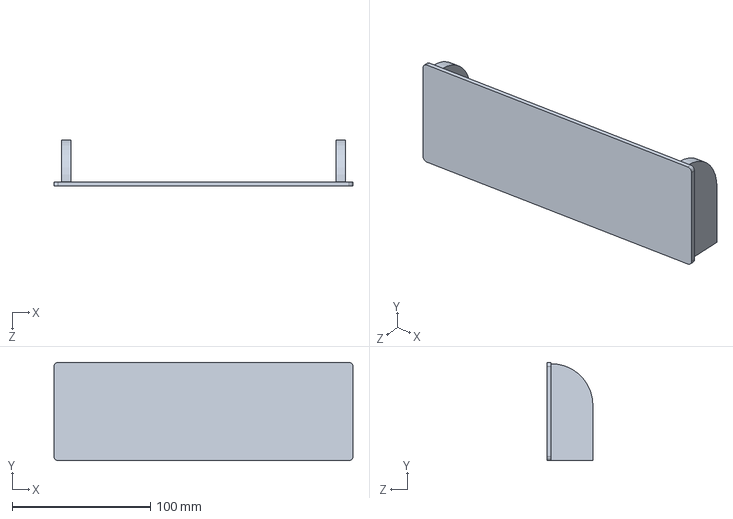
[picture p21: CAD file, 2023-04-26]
3D Modeling/backstand.SLDPRT
215.9 x 71.0 x 33.1 mm

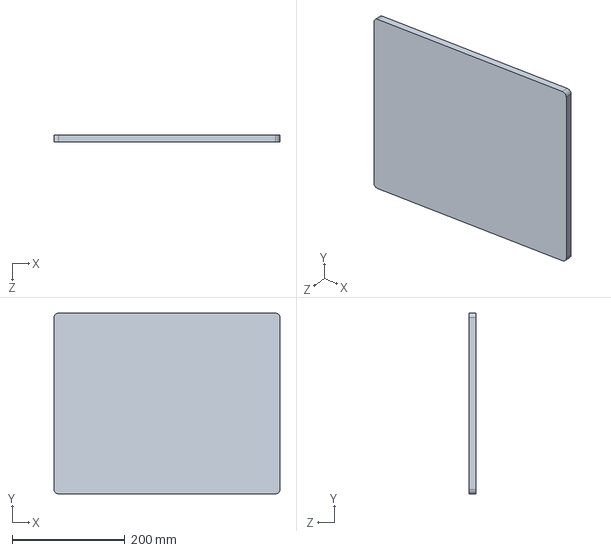
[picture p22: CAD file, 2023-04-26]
3D Modeling/Base Board1.sldprt
400.0 x 320.0 x 13.0 mm

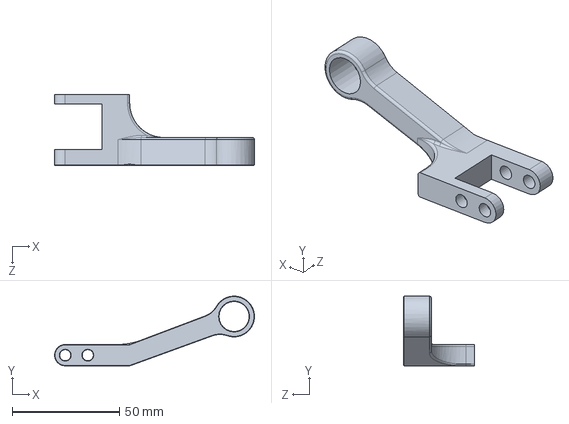
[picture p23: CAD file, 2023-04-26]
3D Modeling/IdlerLever.sldprt
93.0 x 32.5 x 33.0 mm

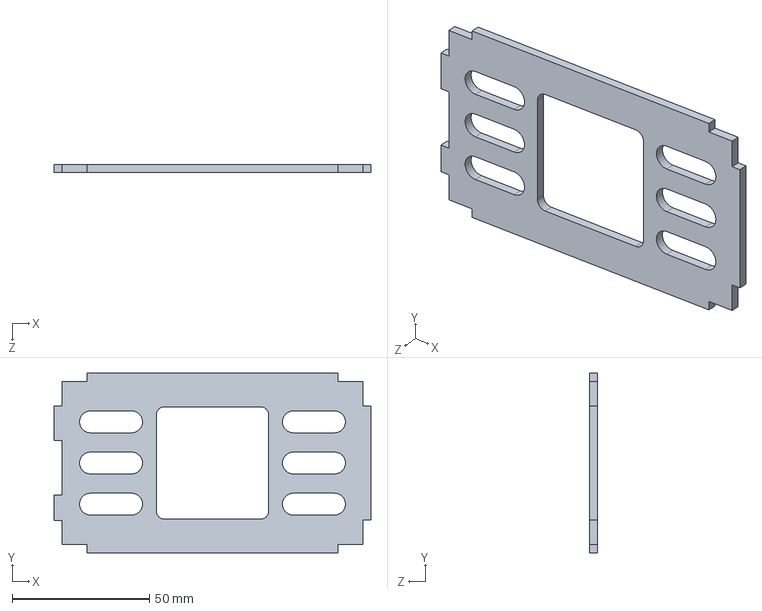
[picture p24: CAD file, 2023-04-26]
3D Modeling/arduinocase2.SLDPRT
115.6 x 65.6 x 3.00 mm

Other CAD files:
3D Modeling/Bic Pen Adapter.sldprt
3D Modeling/Pen Lifter Bar.sldprt
3D Modeling/Base Board.sldprt
3D Modeling/5x11x4 Bearing.sldprt
3D Modeling/605zz idler.sldprt
3D Modeling/SheetOfPaper.sldprt
3D Modeling/605ZZ Bearing.sldprt
3D Modeling/Writing Surface.sldprt
3D Modeling/NEMA-17_38mm.sldprt
3D Modeling/GritDrum.sldprt
3D Modeling/5x35mm Rod.sldprt
3D Modeling/NEMA-17_38mm_23mm.sldprt
3D Modeling/Arduino_Uno_CNC_Shield_V3_1.sldprt
3D Modeling/FeedTable.sldprt
3D Modeling/10mmRod.sldprt
3D Modeling/40x40mmFan.sldprt
3D Modeling/5mmShaftConnector.sldprt
3D Modeling/5x45mm Rod.sldprt
3D Modeling/BearingIdler.sldprt
3D Modeling/DriveWheelShaft.sldprt
3D Modeling/FANArduinoBoxLongTall.sldprt
3D Modeling/FeedTableSupport.sldprt
3D Modeling/GritWheelAdapter.sldprt
3D Modeling/IdlerShaftCap.sldprt
3D Modeling/Left Side Frame.sldprt
3D Modeling/Mirrored IdlerLever.sldprt
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

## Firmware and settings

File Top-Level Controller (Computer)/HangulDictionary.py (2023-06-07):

import math
import matplotlib.pyplot as plt

class Hangul:
    def __init__(self):
        #단위: mm
        #초성 모음
        self.g = [(0, 0, False), (0, 0, True), (1, 0, True), (1, 1, True), (1, 1, False)]
        self.kk = [(0, 0, False), (0, 0, True), (1*10/21, 0, True), (1*10/21, 1, True), (1*10/21, 1, False), (1*11/21, 0, False), (1*11/21, 0, True), (1, 0, True), (1, 1, True), (1, 1, False)]
        self.n = [(0, 0, False), (0, 0, True), (0, 1, True), (1, 1, True), (1, 1, False)]
        self.d = [(1, 0, False), (1, 0, True), (0, 0, True),(0, 1, True),(1, 1, True), (1, 1, False)]
        self.tt = [(1*10/21, 0, False), (1*10/21, 0, True), (0, 0, True), (0, 1, True), (1*10/21, 1, True), (1*10/21, 1, False), (1, 0, False), (1, 0, True), (1*11/21, 0, True), (1*11/21, 1, True), (1, 1, True), (1, 1, False)]
        self.r = [(0, 0, False), (0, 0, True), (1, 0, True), (1, 1/2, True), (0, 1/2, True), (0, 1, True), (1, 1, True), (1, 1, False)]
        self.m = [(0, 0, False), (0, 0, True), (1, 0, True), (1, 1, True), (0, 1, True), (0, 0, True), (0, 0, False)]
        self.b = [(0, 0, False), (0, 0, True), (0, 1, True), (1, 1, True), (1, 0, True), (1, 0, False), (0, 1/2, False), (0, 1/2, True), (1, 1/2, True), (1, 1/2, False)]
        self.pp = [(0, 0, False), (0, 0, True), (0, 1, True), (1*10/21, 1, True), (1*10/21, 0, True), (1*10/21, 0, False), (0, 1/2, False), (0, 1/2, True), (1*10/21, 1/2, True), (1*10/21, 1/2, False), (1*11/21, 0, False), (1*11/21, 0, True), (1*11/21, 1, True), (1, 1, True), (1, 0, True), (1, 0, False), (1*11/21, 1/2, False), (1*11/21, 1/2, True), (1, 1/2, True), (1, 1/2, False)]
        self.s = [(1/2, 0, False), (1/2, 0, True), (0, 1, True), (0, 1, False), (1/2, 0, False), (1/2, 0, True), (1, 1, True), (1, 1, False)]
        self.ss = [(1*5/21, 0, False), (1*5/21, 0, True), (0, 1, True), (0, 1, False), (1*5/21, 0, False), (1*5/21, 0, True), (1*10/21, 1, True), (1*10/21, 1, False), (1*16/21, 0, False), (1*16/21, 0, True), (1*11/21, 1, True), (1*11/21, 1, False), (1*16/21, 0, False), (1*16/21, 0, True), (1, 1, True), (1, 1, False)]
        self.sampling = list(range(0, 361, 20))
        self.ng = [(0, 1/2, False)] + [((1/2) + (1/2)*math.cos(math.radians(180-dot)), 1/2 + (1/2)*math.sin(math.radians(dot)), True) for dot in self.sampling] + [(0, 1/2, False)]
        self.j = [(0, 0, False),(0, 0, True),(1, 0, True),(1, 0, False),(1/2, 0, False), (1/2, 0, True), (0, 1, True),(0, 1, False),(1/2, 0, False),(1/2, 0, True),(1, 1, True),(1, 1, False)]
        self.jj = self.resize(self.j + self.offset(self.j, 1.1, 0), 10/21, 1)
        self.ch = [(1*1/5, 0, False),(1*1/5, 0, True),(1*4/5, 0, True),(1*4/5, 0, False),(0, 1*1/6, False),(0, 1*1/6, True),(1, 1*1/6, True),(1, 1*1/6, False),(1/2, 1*1/6, False), (1/2, 1*1/6, True), (0, 1, True),(0, 1, False),(1/2, 1*1/6, False),(1/2, 1*1/6, True),(1, 1, True),(1, 1, False)]
        self.k = [(0, 0, False), (0, 0, True), (1, 0, True),(1, 1, True),(1, 1, False),(0, 1/2, False),(0, 1/2, True),(1, 1/2, True),(1, 1/2, False)]
        self.t = [(1, 0, False), (1, 0, True), (0, 0, True),(0, 1, True),(1, 1, True),(1, 1, False),(0, 1/2, False),(0, 1/2, True),(1, 1/2, True),(1, 1/2, False)]
        self.p = [(0, 0, False), (0, 0, True), (0, 0, True),(1, 0, True),(1, 0, False),(0, 1, False),(0, 1, True),(1, 1, True),(1, 1, False),(1/3, 0, False),(1/3, 0, True),(1/3, 1, True),(1/3, 1, False),(1*2/3, 0, False),(1*2/3, 0, True),(1*2/3, 1, True),(1*2/3, 1, False)]
        self.h = [(1*1/5, 0, False),(1*1/5, 0, True),(1*4/5, 0, True),(1*4/5, 0, False),(0, 1*1/6, False),(0, 1*1/6, True),(1, 1*1/6, True),(1, 1*1/6, False)] + self.offset(self.resize(self.ng, 9/12, 9/12), 0.5 - 9/24, 3/12)
        self.CHOSUNGDICT = {'ㄱ':self.g, 'ㄴ':self.n, 'ㄷ':self.d, 'ㄸ':self.tt, 'ㄹ':self.r, 'ㅁ':self.m, 'ㅂ':self.b, 'ㅃ':self.pp, 'ㅅ':self.s, 'ㅆ':self.ss, 'ㅇ':self.ng, 'ㅈ':self.j, 'ㅉ':self.jj, 'ㅊ':self.ch, 'ㅋ':self.k, 'ㅌ':self.t, 'ㅍ':self.p, 'ㅎ':self.h}
        #중성 모음
        self.a = [(0, 0, False), (0, 0, True),(0, 1, True),(0, 1, False),(0, 1/2, False),(0, 1/2, True),(1, 1/2, True),(1, 1/2, False)]
        self.ae = [(0, 0, False), (0, 0, True), (0, 1, True),(0, 1, False),(1, 0, False),(1, 0, True),(1, 1, True),(1, 1, False),(0, 1/2, False),(0, 1/2, True),(1, 1/2, True),(1, 1/2, False)]
        self.ya = [(0, 0, False), (0, 0, True), (0, 1, True),(0, 1, False),(0, 1/3, False),(0, 1/3, True),(1, 1/3, True),(1, 1/3, False),(0, 1*2/3, False),(0, 1*2/3, True),(1, 1*2/3, True),(1, 1*2/3, False)]
        self.yae = [(0, 0, False), (0, 0, True), (0, 1, True),(0, 1, False),(1, 0, False),(1, 0, True),(1, 1, True),(1, 1, False),(0, 1/3, False),(0, 1/3, True),(1, 1/3, True),(1, 1/3, False),(0, 1*2/3, False),(0, 1*2/3, True),(1, 1*2/3, True),(1, 1*2/3, False)]
        self.eo = [(0, 1/2, False),(0, 1/2, True),(1, 1/2, True),(1, 1/2, False),(1, 0, False), (1, 0, True), (1, 1, True),(1, 1, False)]
        self.e = [(0, 1/2, False),(0, 1/2, True),(1/2, 1/2, True),(1/2, 1/2, False),(1/2, 0, False), (1/2, 0, True), (1/2, 1, True),(1/2, 1, False),(1, 0, False), (1, 0, True), (1, 1, True),(1, 1, False)]
        self.yeo = [(0, 1/3, False),(0, 1/3, True),(1, 1/3, True),(1, 1/3, False),(0, 1*2/3, False),(0, 1*2/3, True),(1, 1*2/3, True),(1, 1*2/3, False),(1, 0, False), (1, 0, True), (1, 1, True),(1, 1, False),]
        self. ye = [(0, 1/3, False),(0, 1/3, True),(1/2, 1/3, True),(1/2, 1/3, False),(0, 1*2/3, False),(0, 1*2/3, True),(1/2, 1*2/3, True),(1/2, 1*2/3, False),(1/2, 0, False), (1/2, 0, True), (1/2, 1, True),(1/2, 1, False),(1, 0, False), (1, 0, True), (1, 1, True),(1, 1, False),]
        self.o = [(1/2, 0, False), (1/2, 0, True),(1/2, 1, True),(1/2, 1, False),(0, 1, False),(0, 1, True),(1, 1, True),(1, 1, False)]
        self.wa = self.offset(self.resize(self.o, 4/5, 1/5), 0, 6/10) + self.offset(self.resize(self.a, 1/5, 1), 4/5, 0)
        self.wae = self.offset(self.resize(self.o, 4/5, 1/5), 0, 6/10) + self.offset(self.resize(self.ae, 1/5, 1), 4/5, 0)
        self.yo = [(1/3, 0, False), (1/3, 0, True),(1/3, 1, True),(1/3, 1, False),(1*2/3, 0, False), (1*2/3, 0, True),(1*2/3, 1, True),(1*2/3, 1, False),(0, 1, False),(0, 1, True),(1, 1, True),(1, 1, False)]
        self.u = [(0, 0, False),(0, 0, True),(1, 0, True),(1, 0, False),(1/2, 0, False), (1/2, 0, True),(1/2, 1, True),(1/2, 1, False)]
        self.wo = self.offset(self.resize(self.u, 4/5, 3/10), 0, 7/10) + [(1/2, 17/20, False), (1/2, 17/20, True), (4/5, 17/20, True), (4/5, 17/20, False), (4/5, 0, False), (4/5, 0, True), (4/5, 1, True), (4/5, 1, False)]
        self.we = self.offset(self.resize(self.u, 4/5, 3/10), 0, 7/10) + [(1/2, 17/20, False), (1/2, 17/20, True), (4/5, 17/20, True), (4/5, 17/20, False), (4/5, 0, False), (4/5, 0, True), (4/5, 1, True), (4/5, 1, False), (1, 0, False), (1, 0, True), (1, 1, True), (1, 1, False)]
        self.yu = [(0, 0, False), (0, 0, True),(1, 0, True),(1, 0, False),(1/3, 0, False), (1/3, 0, True),(1/3, 1, True),(1/3, 1, False),(1*2/3, 0, False), (1*2/3, 0, True),(1*2/3, 1, True),(1*2/3, 1, False)]
        self.eu = [(0, 1/2, False),(0, 1/2, True),(1, 1/2, True),(1, 1/2, False)]
        self.i = [(1/2, 0, False),(1/2, 0, True),(1/2, 1, True),(1/2, 1, False)]
        self.oe = self.offset(self.resize(self.o, 4/5, 1/5), 0, 6/10) + self.offset(self.resize(self.i, 1/5, 1), 7/10, 0)
        self.wi = self.offset(self.resize(self.u, 4/5, 3/10), 0, 7/10) + self.offset(self.resize(self.i, 1/5, 1), 7/10, 0)
        self.ui = self.offset(self.resize(self.eu, 4/5, 3/10), 0, 6/10) + self.offset(self.resize(self.i, 1/5, 1), 7/10, 0)
        self.JUNGSUNGDICT = {'ㅏ':self.a, 'ㅐ':self.ae, 'ㅑ':self.ya, 'ㅒ':self.yae, 'ㅓ':self.eo, 'ㅔ':self.e, 'ㅕ':self.yeo, 'ㅖ':self.ye, 'ㅗ':self.o, 'ㅘ':self.wa, 'ㅙ':self.wae, 'ㅚ':self.oe, 'ㅛ':self.yo, 'ㅜ':self.u, 'ㅝ':self.wo, 'ㅞ':self.we, 'ㅟ':self.wi, 'ㅠ':self.yu, 'ㅡ':self.eu, 'ㅢ':self.ui, 'ㅣ':self.i}
        #종성 모음
        self.gs = self.resize(self.g + self.offset(self.s, 1.1, 0), 10/21, 1)
        self.nj = self.resize(self.n + self.offset(self.j, 1.1, 0), 10/21, 1)
        self.nh = self.resize(self.n + self.offset(self.h, 1.1, 0), 10/21, 1)
        self.rg = self.resize(self.r + self.offset(self.g, 1.1, 0), 10/21, 1)
        self.rm = self.resize(self.r + self.offset(self.m, 1.1, 0), 10/21, 1)
        self.rb = self.resize(self.r + self.offset(self.b, 1.1, 0), 10/21, 1)
        self.rs = self.resize(self.r + self.offset(self.s, 1.1, 0), 10/21, 1)
        self.rt = self.resize(self.r + self.offset(self.t, 1.1, 0), 10/21, 1)
        self.rp = self.resize(self.r + self.offset(self.p, 1.1, 0), 10/21, 1)
        self.rh = self.resize(self.r + self.offset(self.h, 1.1, 0), 10/21, 1)
        self.bs = self.resize(self.b + self.offset(self.s, 1.1, 0), 10/21, 1)
        self.JONGSUNGDICT = {'ㄳ':self.gs, 'ㄵ':self.nj, 'ㄶ':self.nh, 'ㄺ':self.rg, 'ㄻ':self.rm, 'ㄼ':self.rb, 'ㄽ':self.rs, 'ㄾ':self.rt, 'ㄿ':self.rp, 'ㅀ':self.rh, 'ㅄ':self.bs, 'ㄱ':self.g, 'ㄴ':self.n, 'ㄷ':self.d, 'ㄸ':self.tt, 'ㄹ':self.r, 'ㅁ':self.m, 'ㅂ':self.b, 'ㅃ':self.pp, 'ㅅ':self.s, 'ㅆ':self.ss, 'ㅇ':self.ng, 'ㅈ':self.j, 'ㅉ':self.jj, 'ㅊ':self.ch, 'ㅋ':self.k, 'ㅌ':self.t, 'ㅍ':self.p, 'ㅎ':self.h}

    def shower(self, word):
        x = []
        y = []
        z = []
        for dot in word:
            x.append(dot[0])
            y.append(dot[1])
            z.append(dot[2])
        ax = plt.figure(figsize=(5,5)).add_subplot(projection='3d')
        ax.axis([0, 1, 1, 0])
        ax.plot(x, y, z)
        ax.set_title('word trajectory 3d plot')

    def stringShower(self, size ,wordnum, string):
        x = []
        y = []
        z = []
        for dot in string:
            x.append(dot[0])
            y.append(dot[1])
            z.append(dot[2])
        ax = plt.figure().add_subplot(projection='3d')
        ax.axis([0, 210, 297, 0])
        ax.plot(x, y, z)
        ax.set_title("string trajectory 3d plot")

    def offset(self, word, x, y):
        word = word.copy()
        for dot in range(0,len(word)):
            word[dot] = list(word[dot])
        for dot in range(0, len(word)):
            word[dot][0] = word[dot][0] + x
            word[dot][1] = word[dot][1] + y
        for dot in range(0,len(word)):
            word[dot] = tuple(word[dot])
        return word
    
    def resize(self, word, xscale, yscale):
        word = word.copy()
        for dot in range(0,len(word)):
            word[dot] = list(word[dot])
        for dot in range(0, len(word)):
            word[dot][0] = word[dot][0] * xscale
            word[dot][1] = word[dot][1] * yscale
        for dot in range(0,len(word)):
            word[dot] = tuple(word[dot])
        return word
    
    def string_dot(self, size, chars):
        string_dot_list = []
        i = 0
        yoffset = 0
        for char in chars:
            if char != 'space':
                if i+size > 165:
                    yoffset = yoffset + 1.5*size
                    i = 0
                char = self.offset(char, i, yoffset)
                string_dot_list = string_dot_list + char
                i = i + 1.1*size
            else:
                i = i + 1.1*size
        string_dot_list = string_dot_list + [(0, yoffset + 1.5*size, False)]
        return string_dot_list

    def Type1(self, size, word1, word2):
        word1 = self.resize(word1, size*55/100, size*4/5)
        word2 = self.resize(word2, size*35/100, size*1)
        word1 = self.offset(word1, 0, size*1/10)
        word2 = self.offset(word2, size*65/100, 0)
        return self.resize(word1+word2, 1, 1)

    def Type2(self, size, word1, word2, word3):
        temp = self.Type1(1, word1, word2)
        temp = self.resize(temp, size, size*55/100)
        word3 = self.resize(word3, size*4/5, size*35/100)
        word3 = self.offset(word3, size*1/10, size*65/100)
        return self.resize(temp+word3, 1, 1)

    def Type3(self, size, word1, word2):
        word1 = self.resize(word1, size*4/5, size*55/100)
        word2 = self.resize(word2, size*1, size*35/100)
        word1 = self.offset(word1, size*1/10, 0)
        word2 = self.offset(word2, 0, size*65/100)
        return self.resize(word1+word2, 1, 1)

    def Type4(self, size, word1, word2, word3):
        temp = self.Type3(1, word1, word2)
        temp = self.resize(temp, size, size*65/100)
        word3 = self.resize(word3, size*4/5, size*25/100)
        word3 = self.offset(word3, size*1/10, size*75/100)
        return self.resize(temp+word3, 1, 1)

    def Type5(self, size, word1, word2):
        word1 = self.resize(word1, size*0.6, size*0.5)
        word1 = self.offset(word1, size*0.1, size*0.1)
        word2 = self.resize(word2, size, size)
        return self.resize(word1+word2, 1, 1)

    def Type6(self, size, word1, word2, word3):
        temp = self.Type5(1, word1, word2)
        temp = self.resize(temp, size, size*65/100)
        word3 = self.resize(word3, size*7/10, size*25/100)
        word3 = self.offset(word3, size*1/10, size*75/100)
        return self.resize(temp+word3, 1, 1)
    
    def TrajectoryMaker(self, size, dividedHangul):
        Hangul.TrajectoryList = []
        for word in dividedHangul:
            if word[0] == 'Space':
                Hangul.TrajectoryList.append('space')
            if word[0] == 'Type1':
                Hangul.TrajectoryList.append(self.Type1(size, self.CHOSUNGDICT[word[1]], self.JUNGSUNGDICT[word[2]]))
            elif word[0] == 'Type2':
                Hangul.TrajectoryList.append(self.Type2(size, self.CHOSUNGDICT[word[1]], self.JUNGSUNGDICT[word[2]], self.JONGSUNGDICT[word[3]]))
            elif word[0] == 'Type3':
                Hangul.TrajectoryList.append(self.Type3(size, self.CHOSUNGDICT[word[1]], self.JUNGSUNGDICT[word[2]]))
            elif word[0] == 'Type4':
                Hangul.TrajectoryList.append(self.Type4(size, self.CHOSUNGDICT[word[1]], self.JUNGSUNGDICT[word[2]], self.JONGSUNGDICT[word[3]]))
            elif word[0] == 'Type5':
                Hangul.TrajectoryList.append(self.Type5(size, self.CHOSUNGDICT[word[1]], self.JUNGSUNGDICT[word[2]]))
            elif word[0] == 'Type6':
                Hangul.TrajectoryList.append(self.Type6(size, self.CHOSUNGDICT[word[1]], self.JUNGSUNGDICT[word[2]], self.JONGSUNGDICT[word[3]]))
        return self.string_dot(size, Hangul.TrajectoryList)

if __name__ == '__main__':
    H = Hangul()
    # Combine
    H.stringShower(1, 3, H.string_dot(1, [H.Type2(1, H.k, H.eo, H.m), H.Type3(1, H.p, H.yu), H.Type1(1, H.t, H.eo)]))
    H.stringShower(1, 2, H.string_dot(1, [H.Type2(1, H.j, H.eo, H.r), H.Type1(1, H.d, H.ae)]))
    H.stringShower(1, 2, H.string_dot(1, [H.Type1(1, H.ng, H.a), H.Type1(1, H.h, H.a)]))
    H.stringShower(1, 4, H.string_dot(1, [H.Type1(1, H.d, H.i), H.Type1(1, H.j, H.i), H.Type3(1, H.s, H.eu), H.Type3(1, H.t, H.eu)]))
    H.stringShower(1, 4, H.string_dot(1, [H.Type3(1, H.s, H.u), H.Type4(1, H.n, H.eu, H.ng), H.Type4(1, H.t, H.eu, H.g), H.Type2(1, H.g, H.a, H.ng)]))
    H.stringShower(1, len([['Type2', 'ㅂ', 'ㅐ', 'ㄱ'], ['Type2', 'ㅁ', 'ㅣ', 'ㄴ'], ['Type2', 'ㅎ', 'ㅕ', 'ㄱ']]), H.TrajectoryMaker(1, [['Type2', 'ㅂ', 'ㅐ', 'ㄱ'], ['Type2', 'ㅁ', 'ㅣ', 'ㄴ'], ['Type2', 'ㅎ', 'ㅕ', 'ㄱ']]))

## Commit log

2023-04-26 Hardware, stepper test added
    [10mmRod.sldprt, 40x40mmFan.sldprt, 5mmShaftConnector.sldprt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]
2023-06-07 Hangul Pen Plotter prototype complete
2023-06-22 Arrange For Publishing
    [10mmRod.sldprt, 40x40mmFan.sldprt, 5mmShaftConnector.sldprt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]
